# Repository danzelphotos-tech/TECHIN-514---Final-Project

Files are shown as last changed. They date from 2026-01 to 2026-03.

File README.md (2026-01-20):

# Vibe Bot – Interactive Music-Responsive Desk Robot

Vibe Bot is a wireless, music-responsive desk robot that senses ambient audio to estimate the tempo (BPM) of music and visualizes it through a mechanical gauge, animated facial display, and dynamic lighting. The system consists of a separate sensing device and display device that communicate wirelessly.

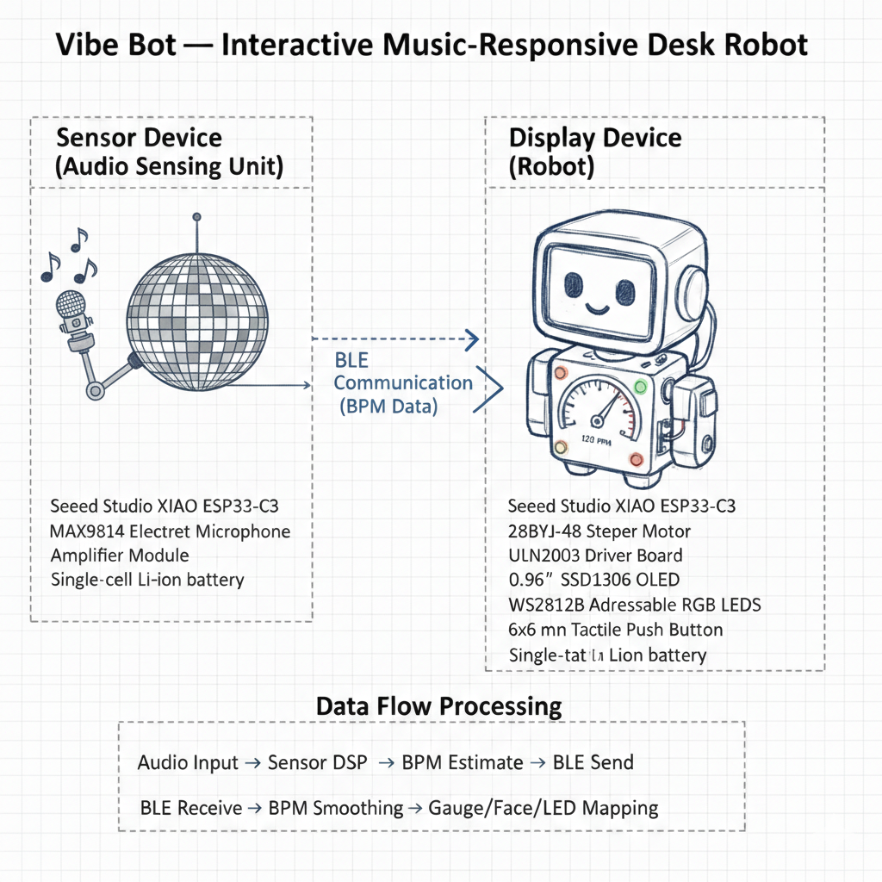
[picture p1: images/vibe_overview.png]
Overview sketch


## Sensor Device (Audio Sensing Unit)

The sensor device is a compact, battery-powered module placed near the music source. It uses a microphone to capture ambient audio, runs DSP to estimate BPM, and transmits BPM data wirelessly to the display device.

Parts (sensor device):
- Microcontroller: Seeed Studio XIAO ESP32-C3 (ESP32-C3)
- Microphone: INMP441 (I2S MEMS microphone) 

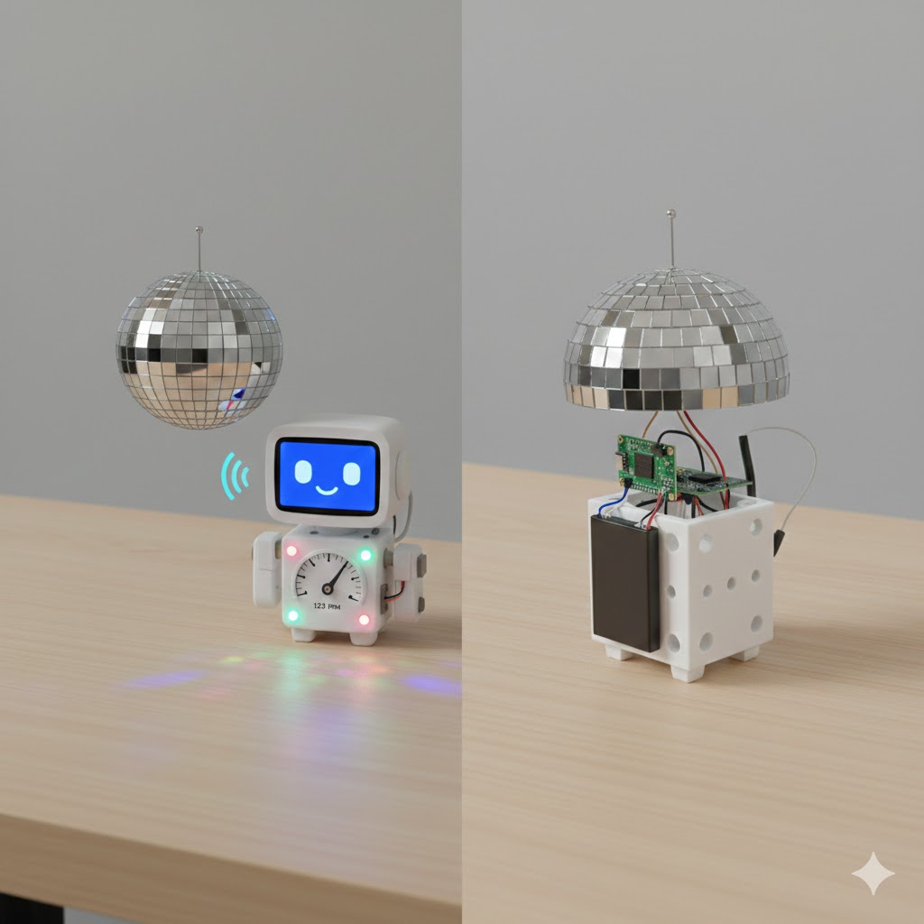
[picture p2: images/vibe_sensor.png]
Sensor device sketch


## Display Device (Robot)

The display device is a 3D-printed desktop robot that receives BPM data and visualizes it using a stepper-motor gauge needle, at least one LED, and a button for interaction (mode selection / calibration). The face is shown using an OLED display, and the LEDs provide "party lights" effects.

Parts (display device):
- Microcontroller: Seeed Studio XIAO ESP32-C3 (ESP32-C3)
- Stepper motor: 28BYJ-48
- Stepper driver: ULN2003 driver board 
- OLED: 0.96" SSD1306 I2C OLED
- LEDs: WS2812B addressable LEDs
- Button: 6x6mm tactile pushbutton

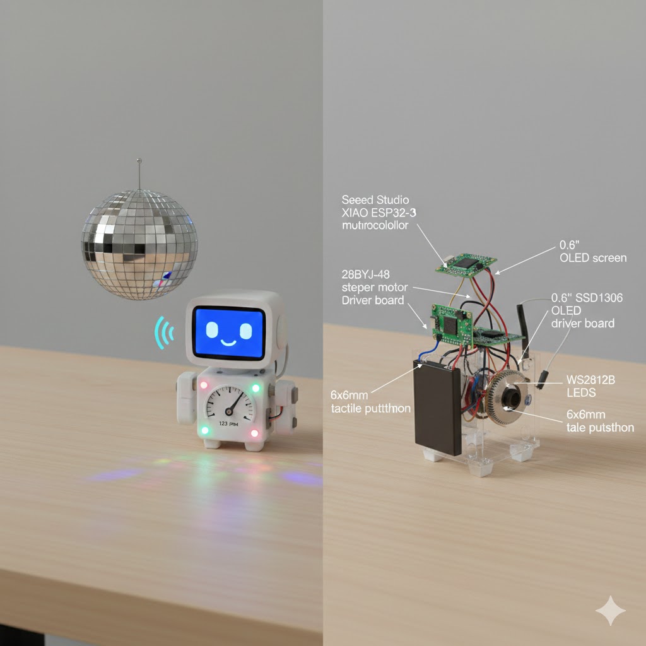
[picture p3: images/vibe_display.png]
Display device sketch


## Communication and Data Flow

The sensor device estimates BPM from audio and sends BPM (and optional confidence) over BLE to the display device. The display device smooths incoming BPM values and maps them to gauge needle position, facial animation states, and LED patterns.

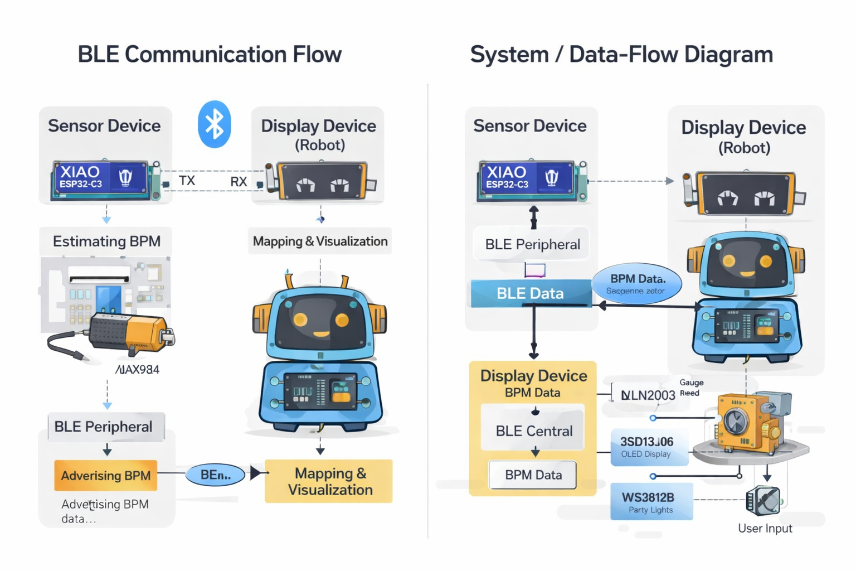
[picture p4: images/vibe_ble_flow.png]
BLE communication & diagram


## Datasheets

All component datasheets are available in the `datasheets/` folder, including:
- ESP32-C3 microcontroller
- MAX9814 microphone amplifier
- SSD1306 OLED display
- WS2812B RGB LEDs
- 28BYJ-48 stepper motor
- ULN2003 stepper driver

### Selected Components (Final)

Sensor Device:
- Microcontroller: Seeed Studio XIAO ESP32-C3
- Microphone: MAX9814 Electret Microphone Amplifier Module
- Power: Single-cell Li-ion battery

Display Device:
- Microcontroller: Seeed Studio XIAO ESP32-C3
- Stepper Motor: 28BYJ-48
- Stepper Driver: ULN2003
- Display: 0.96" SSD1306 OLED (I2C)
- LEDs: WS2812B addressable RGB LEDs
- User Input: 6x6 mm tactile push button
- Power: Single-cell Li-ion battery with onboard regulation

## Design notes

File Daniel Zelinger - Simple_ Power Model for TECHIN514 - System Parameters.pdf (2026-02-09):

System Parameters (defined by hardware) | Profiles (usage of each component mode - defined by software and usage)
form the datasheets
"off" | "sensing" | "interactive"

Processor
Active | 120 mW | 0% | 10% | 50%
Idle | 20 mW | 0% | 20% | 30%
Sleep | 1 mW | 100% | 70% | 20%
LED On | 5 mW | 0% | 5% | 50%
Sensor On | 10 mW | 0% | 10% | 80%
Idle | 2 mW | 0% | 90% | 20%
Off | 0 mW | 100% | 0% | 0%
Display On | 25 mW | 0% | 20% | 100%
Off (leakage) | 1 mW | 100% | 80% | 0%
Radio Data Rate | 300 bps | 0% | 0% | 0% | Total power in profile (mw) | Maximum Time
Standby Power | 5 mW | 98% | 95% | 90% | "off" | 7.0009696 mW | 223.9 hours
TX Power | 250 mW | 0% | 1% | 5% | "sensing" | 34.000764 mW | 46.1 hours RX Power | 120 mW | 0% | 1% | 5% | "interactive" | 125.100288 mW | 12.5 hours
16 | 7 | 1 hours/day typical usage | Effective Battery Capacity Battery | 1567.5 mW*h Capacity | 500 mAh Nominal Voltage | 3 V | Days of Use | 3.30 days Regulator Efficiency | 95% | Hours of Use | 79.18 hours
Days of use is calculated by combining the average daily energy REFLECTIONS : WHAT DID YOU LEARN FROM ANALYZING YOUR POWER. TALK ABOUT SOME POTENTIAL TRADEOFFS. | consumption across off, sensing, and interactive modes based on expected daily usage hours.

I determined the days of use by estimating how the device would typically be used each day and dividing that time between off, sensing, and interactive modes. I then calculated the average daily energy consumption using the power values of each component and how often they are active in each mode.

I chose the battery size by balancing how long the device should run with its size and cost. For the sensor device, a 500 mAh battery allows the device to operate for multiple days while staying small and lightweight. The display device uses more power because of the OLED screen and user interaction, so a larger 1000 mAh battery is more appropriate.

To improve the user experience, power consumption could be reduced by using deeper sleep modes, sending data less frequently, lowering the LED brightness, or using BLE instead of Wi Fi. These changes would require more software effort and design decisions, but they would result in longer battery life and a more comfortable and usable device.

DATASHEETS

ESP32 | | https://www.espressif.com/sites/default/files/documentation/esp32-c3_datasheet_en.pdf
LED — Standard | | https://www.vishay.com/docs/83171/tlms1100.pdf
SENSOR - INMP441 | https://invensense.tdk.com/wp-content/uploads/2015/02/INMP441.pdf Display — SSD1306 OLEDhttps://cdn-shop.adafruit.com/datasheets/SSD1306.pdf Radio (ESP32C3) | https://www.espressif.com/sites/default/files/documentation/esp32-c3_technical_reference_manual_en.pdf
Batteries | https://www.adafruit.com/product/1578
| https://www.adafruit.com/product/258

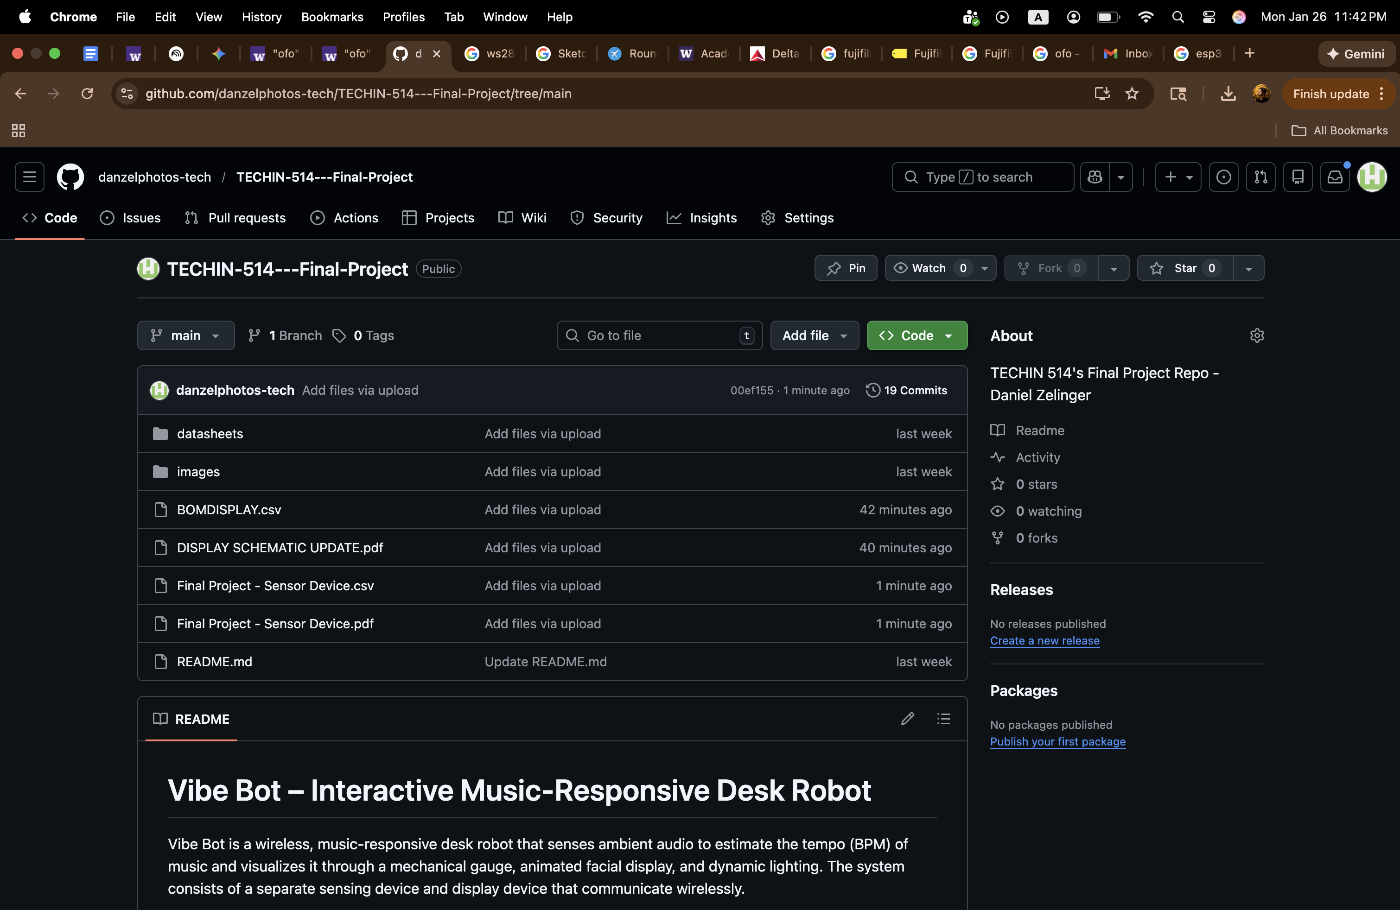
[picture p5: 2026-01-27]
GitHub SS 1:26:26.png

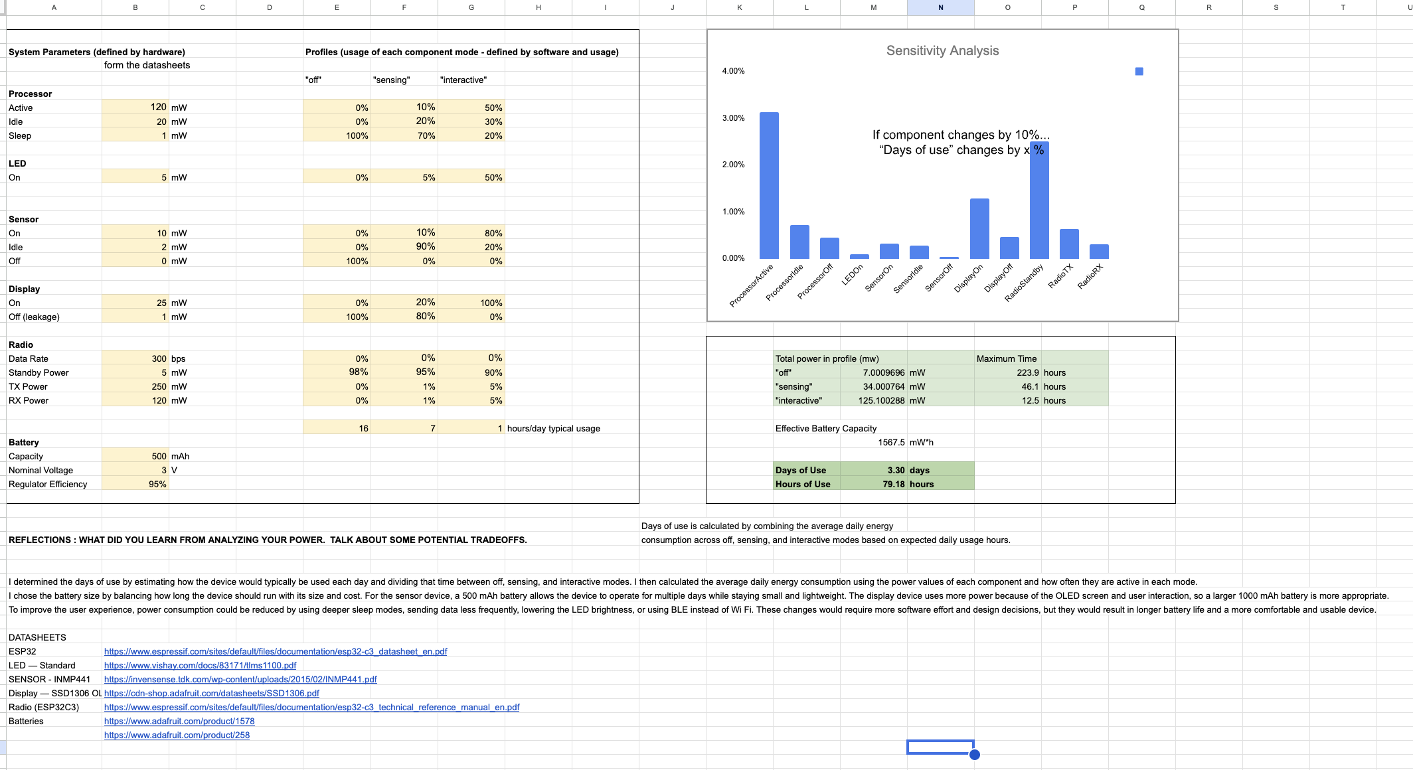
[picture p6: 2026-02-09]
Battery Life Estimate DZ.png

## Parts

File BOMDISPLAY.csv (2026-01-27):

Reference | Qty | Value | DNP | Exclude from BOM | Exclude from Board | Footprint | Datasheet
Brd1 | 1 | SSD1306
C1 | 1 | 470 µF |  |  |  |  | ~
D1 | 1 | WS2812B |  |  |  | LED_SMD:LED_WS2812B_PLCC4_5.0x5.0mm_P3.2mm | https://cdn-shop.adafruit.com/datasheets/WS2812B.pdf
J1 | 1 | Conn_01x05 |  |  |  |  | ~
J_BATT? | 1 | Conn_01x02 |  |  |  |  | ~
R1 | 1 | 330 Ω |  |  |  |  | ~
SW1 | 1 | SW_Push |  |  |  |  | ~
U1 | 1 | XIAO ESP32C3 |  |  |  | XIAO_ESP32C3:xiao_esp32c3 | https://files.seeedstudio.com/wiki/Seeed-Studio-XIAO-ESP32/esp32-c3_datasheet.pdf
U2 | 1 | ULN2003 |  |  |  |  | http://www.ti.com/lit/ds/symlink/uln2003a.pdf

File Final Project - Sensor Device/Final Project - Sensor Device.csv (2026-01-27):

Reference | Qty | Value | DNP | Exclude from BOM | Exclude from Board | Footprint | Datasheet
C_MIC? | 1 | 0.1 µF ceramic capacitor |  |  |  |  | ~
INMP441 | 1 | ~
J1 | 1 | J_BATT |  |  |  |  | ~
U1 | 1 | XIAO ESP32C3 |  |  |  | XIAO_ESP32C3:xiao_esp32c3 | https://files.seeedstudio.com/wiki/Seeed-Studio-XIAO-ESP32/esp32-c3_datasheet.pdf

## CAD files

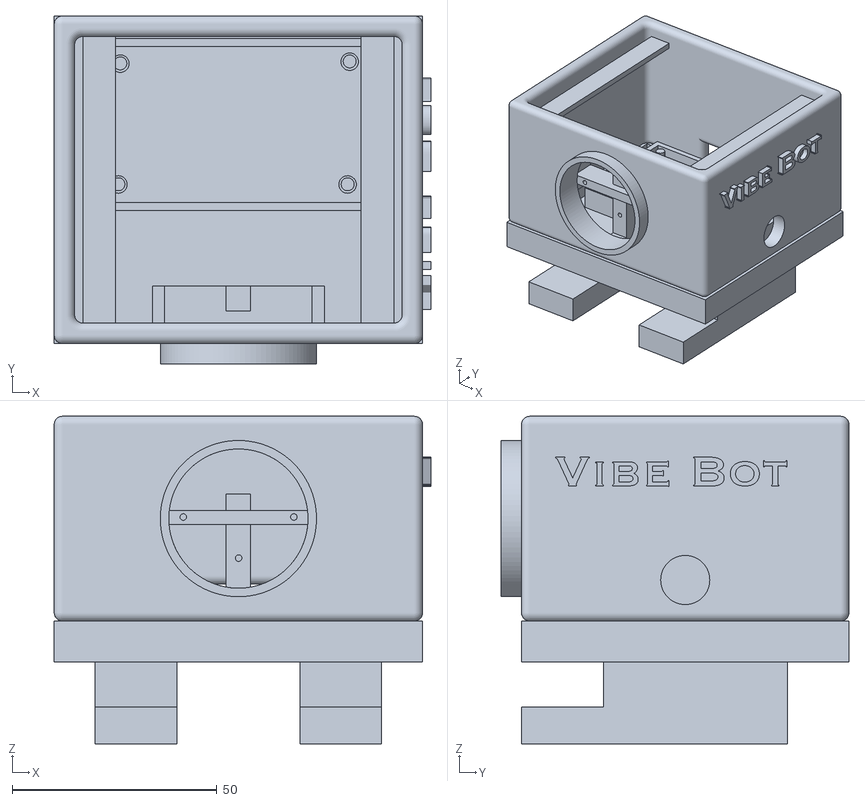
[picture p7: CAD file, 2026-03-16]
Display Device/Vibe Bot - Display Device - DZ STL.stl
92.0 x 85.0 x 80.0

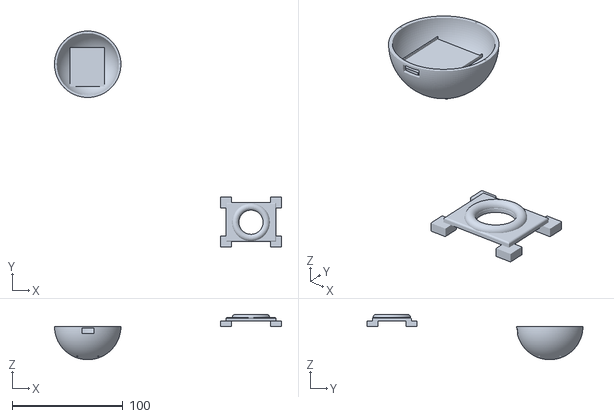
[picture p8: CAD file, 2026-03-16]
Final Project - Sensor Device/Final Project - Sensor Device Draft 1 DZ.stl
205.0 x 195.0 x 41.0

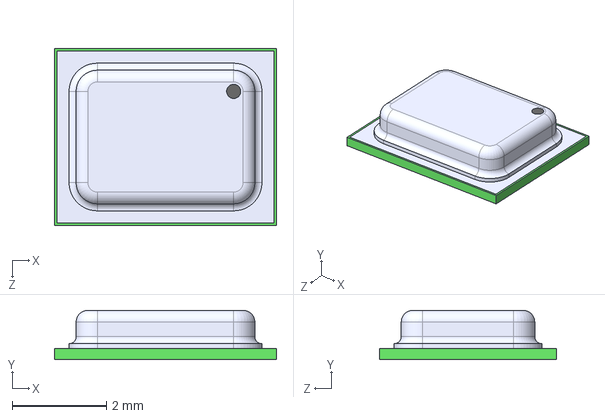
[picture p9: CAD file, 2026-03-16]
Final Project - Sensor Device/INMP441ACEZ-R7/INMP441ACEZ-R7.step
4.72 x 1.05 x 3.76 mm

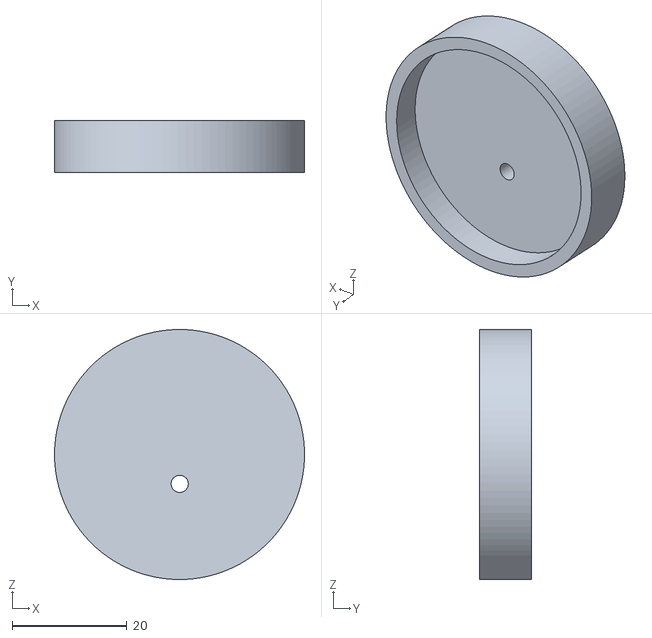
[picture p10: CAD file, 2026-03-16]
Display Device/Vibe Bot - Display Device - DZ - Motor Cap 2.stl
43.5 x 9.00 x 43.5

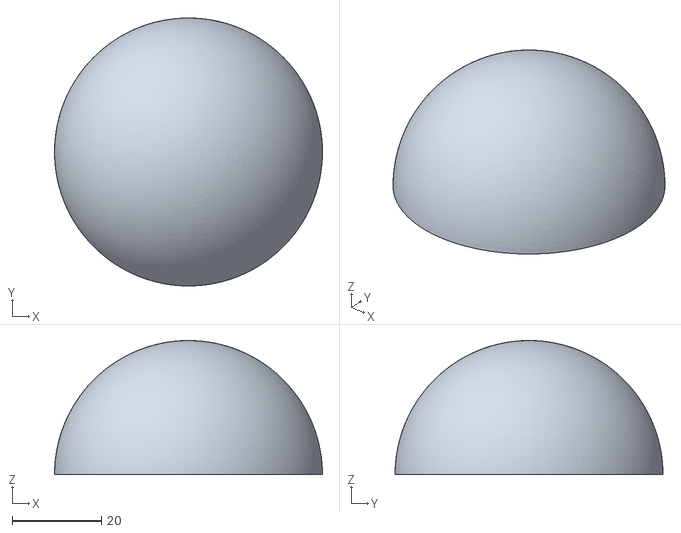
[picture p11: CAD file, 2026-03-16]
Final Project - Sensor Device/Final Project - Sensor Device Top.stl
60.0 x 60.0 x 30.0

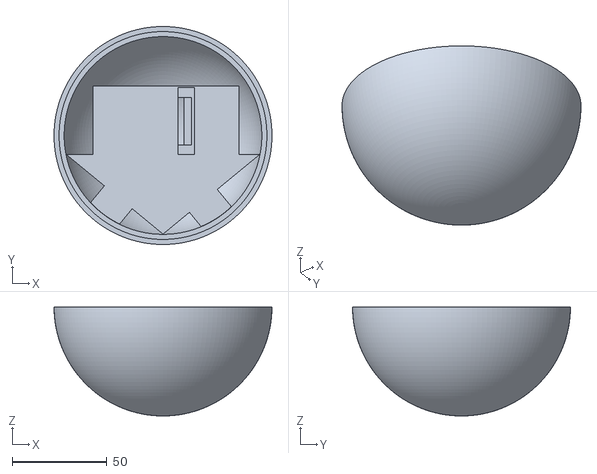
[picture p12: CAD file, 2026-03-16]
Display Device/Final Project - Sensor Device - BOTTOM.stl
115.0 x 115.0 x 57.5

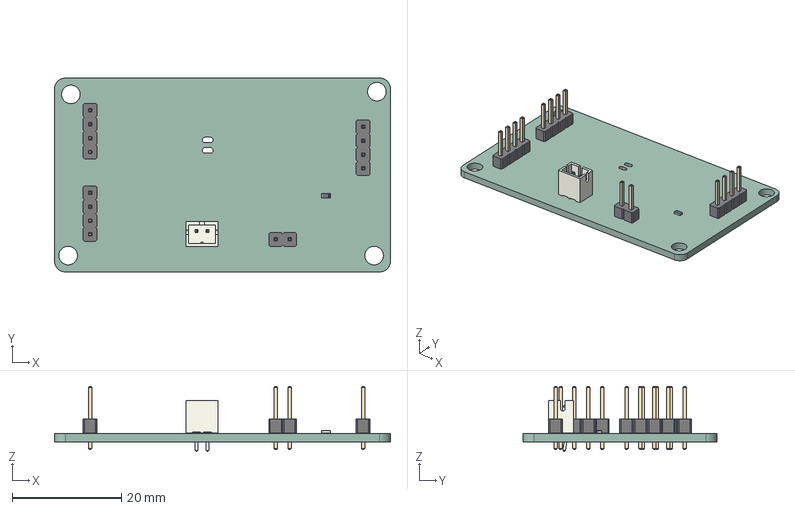
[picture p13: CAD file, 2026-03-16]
Display Device/Vibe Bot - Display Device - DZ.step
61.5 x 35.5 x 11.9 mm
PinHeader_1x04_P2.54mm_Vertical x 3
R_0603_1608Metric
PinHeader_1x02_P2.54mm_Vertical
JST_PH_B2B-PH-K_1x02_P2.00mm_Vertical
Vibe Bot - Display Device - DZ_PCB

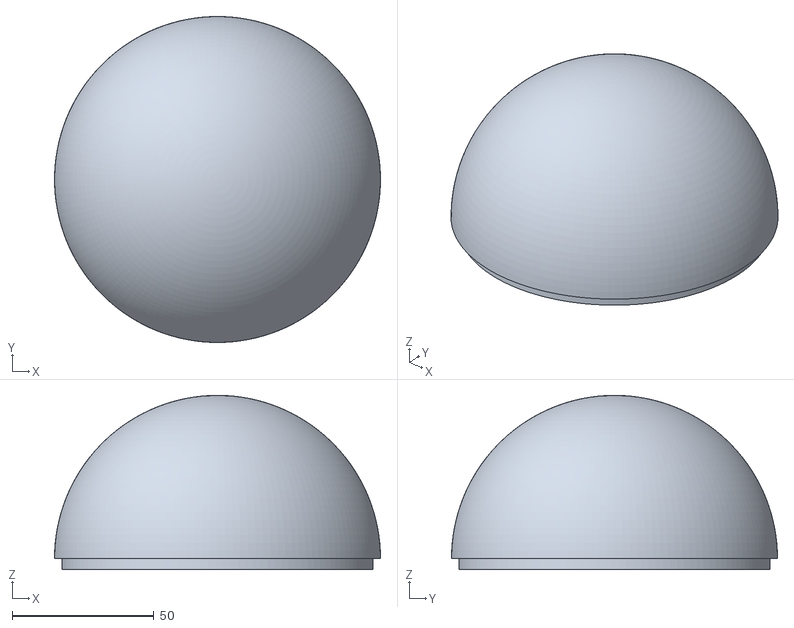
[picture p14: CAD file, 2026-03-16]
Display Device/Final Project - Sensor Device - Final Print_.stl
115.0 x 115.0 x 61.5

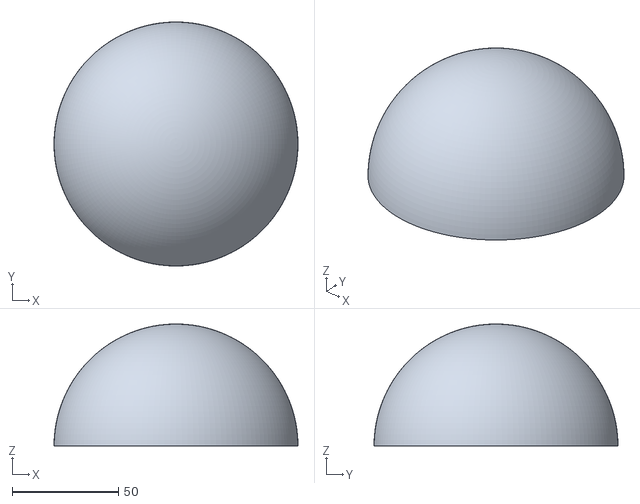
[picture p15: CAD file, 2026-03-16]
Display Device/Final Project - Sensor Device TOP.stl
115.0 x 115.0 x 57.5

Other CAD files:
Display Device/Vibe Bot - Display Device - DZ.stl
Final Project - Sensor Device/Final Project - Sensor Device FUSION F3D.f3z

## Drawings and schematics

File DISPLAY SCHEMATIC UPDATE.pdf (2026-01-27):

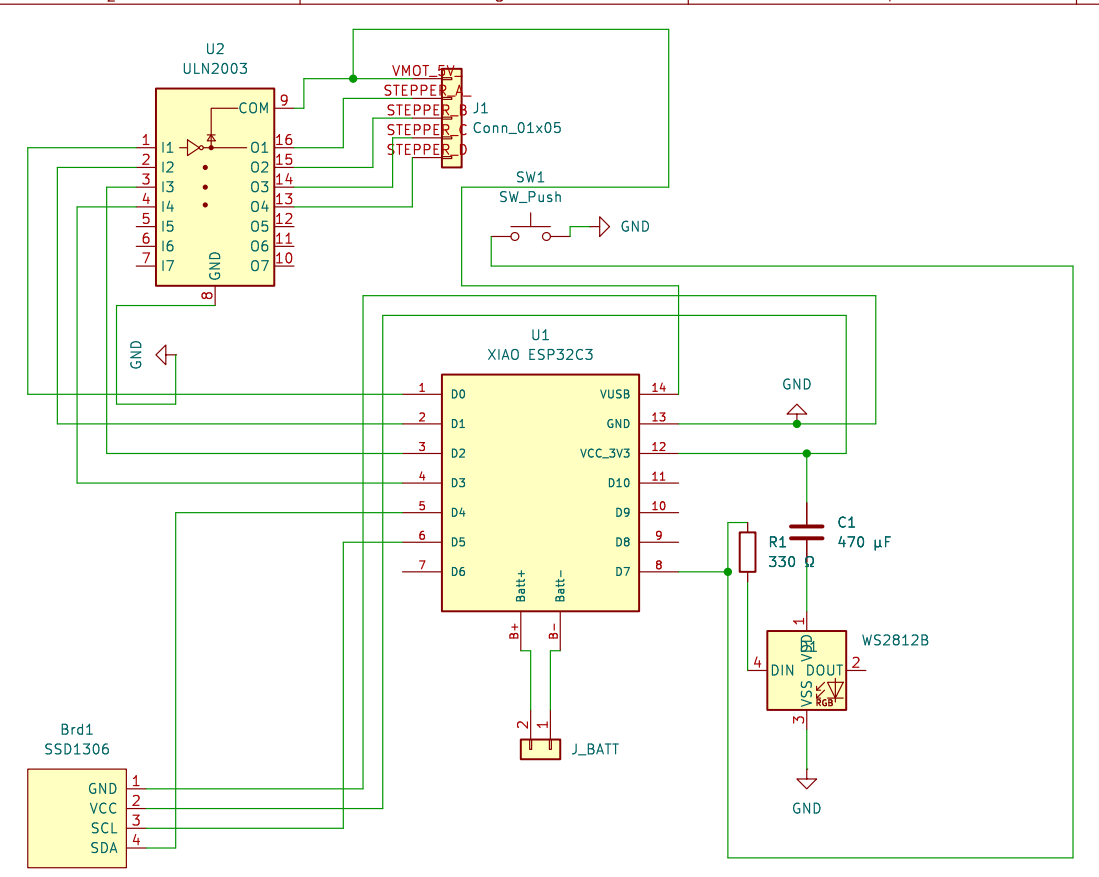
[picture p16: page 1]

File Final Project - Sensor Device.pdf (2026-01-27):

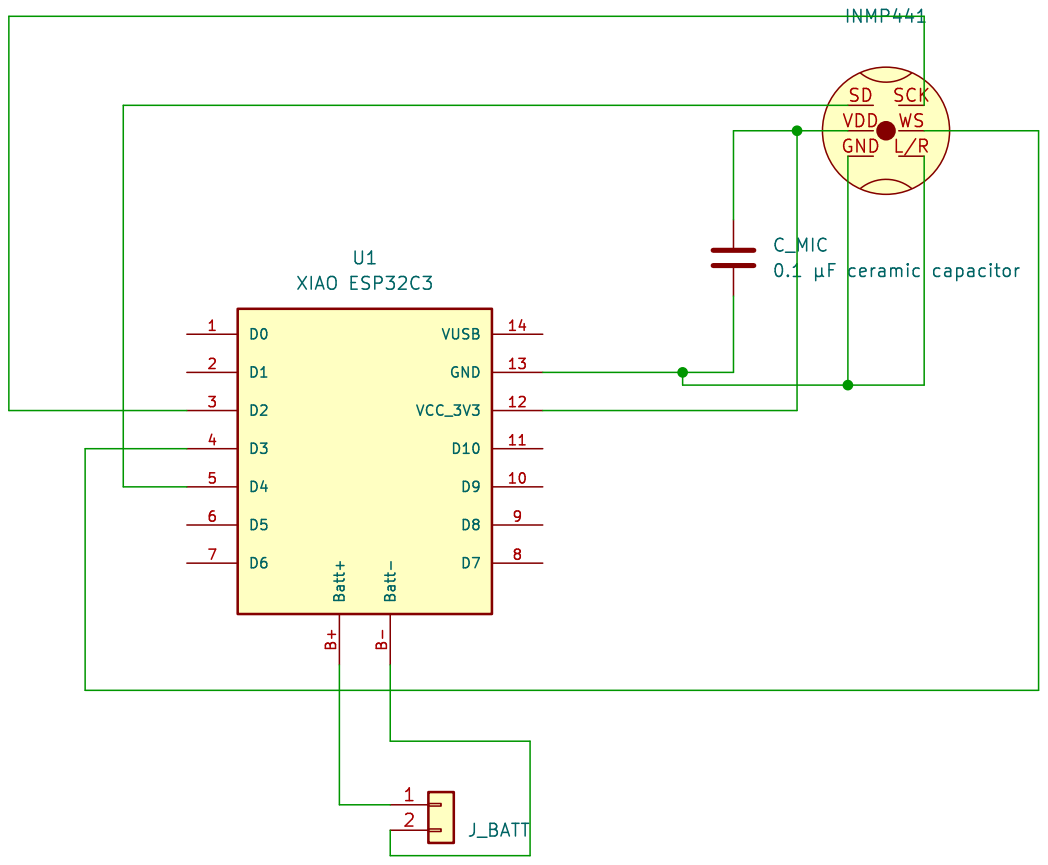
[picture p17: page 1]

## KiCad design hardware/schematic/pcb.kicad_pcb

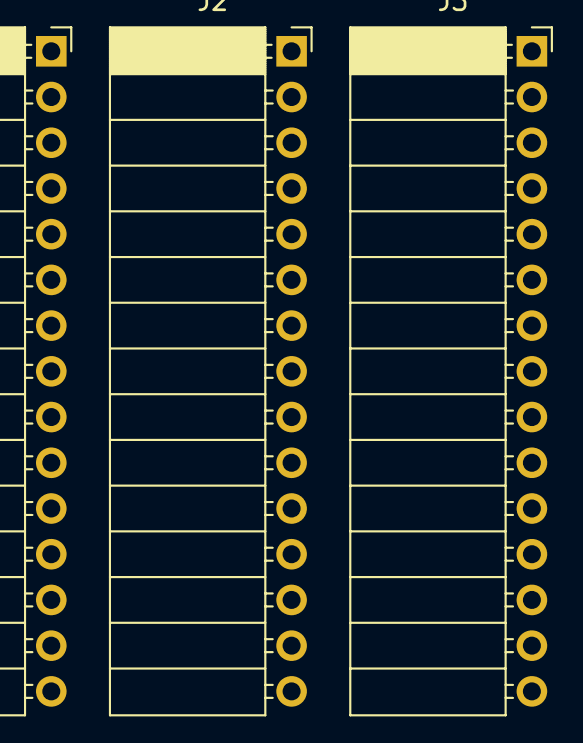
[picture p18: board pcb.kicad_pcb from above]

Board: 2 copper layers, 3 parts (0 on the bottom side), 10 nets, no tracks yet.

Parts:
J1: L; PinSocket_1x15_P2.54mm_Horizontal
J2: R; PinSocket_1x15_P2.54mm_Horizontal
J3: IR; PinSocket_1x15_P2.54mm_Horizontal

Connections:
unnamed: J1.12 (5V), J3.11 (VCC)
unnamed: J1.10 (A6), J3.10 (D8)
unnamed: J2.11 (D2), J3.3 (D1)
unnamed: J2.9 (D4), J3.4 (D2)
unnamed: J2.6 (D7), J3.5 (D3)
unnamed: J2.5 (D8), J3.6 (D4)
unnamed: J2.3 (D10), J3.7 (D5)
unnamed: J2.2 (D11), J3.8 (D6)
unnamed: J2.1 (D12), J3.9 (D7)
unnamed: J2.12 (GND), J3.1 (GND)

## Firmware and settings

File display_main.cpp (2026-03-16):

#include <Arduino.h>
#include <WiFi.h>
#include <esp_now.h>
#include <esp_idf_version.h>
#include <Wire.h>
#include <Adafruit_GFX.h>
#include <Adafruit_SSD1306.h>
#include <Adafruit_NeoPixel.h>
#include <SwitecX25.h>

// ===================== PIN CONFIG =====================
#define OLED_SDA    D4
#define OLED_SCL    D5
#define LED_PIN     D7
#define BUTTON_PIN  D8
#define MOTOR_P1    D0
#define MOTOR_P2    D1
#define MOTOR_P3    D2
#define MOTOR_P4    D3

// ===================== HARDWARE CONSTANTS =====================
#define SCREEN_W    128
#define SCREEN_H    64
#define OLED_ADDR   0x3C
#define NUM_LEDS    16
#define MOTOR_STEPS 945  // X27: 315 deg * 3 steps/deg

// ===================== PACKET (must match sensor) =====================
typedef struct __attribute__((packed)) {
  int bpm;
  int peak;
  int level;
  int beat;
  int activity;
} SensorPacket;

// ===================== VISUAL MODES =====================
enum VisualMode {
  MODE_STANDBY,
  MODE_FACE,
  MODE_BIG_BPM,
  MODE_SYNTH,
  MODE_LASER
};

static const char* modeName(VisualMode m) {
  switch (m) {
    case MODE_STANDBY: return "STANDBY";
    case MODE_FACE:    return "FACE";
    case MODE_BIG_BPM: return "BIG_BPM";
    case MODE_SYNTH:   return "SYNTH";
    case MODE_LASER:   return "LASER";
    default:           return "???";
  }
}

// Deterministic mode cycle when music is playing.
// BIG_BPM appears 3 times per 42-second cycle and cannot be skipped.
struct ModeSlot { VisualMode mode; unsigned long ms; };

static const ModeSlot MODE_CYCLE[] = {
  { MODE_BIG_BPM, 3000 },  // 0  show BPM first thing when music starts
  { MODE_FACE,    5000 },  // 1
  { MODE_FACE,    5000 },  // 2
  { MODE_BIG_BPM, 3000 },  // 3
  { MODE_FACE,    5000 },  // 4
  { MODE_SYNTH,   4000 },  // 5
  { MODE_FACE,    5000 },  // 6
  { MODE_BIG_BPM, 3000 },  // 7
  { MODE_FACE,    5000 },  // 8
  { MODE_LASER,   4000 },  // 9
};
static const int CYCLE_LEN = sizeof(MODE_CYCLE) / sizeof(MODE_CYCLE[0]);

// ===================== HARDWARE OBJECTS =====================
Adafruit_SSD1306 oled(SCREEN_W, SCREEN_H, &Wire, -1);
Adafruit_NeoPixel strip(NUM_LEDS, LED_PIN, NEO_GRB + NEO_KHZ800);
SwitecX25 motor(MOTOR_STEPS, MOTOR_P1, MOTOR_P2, MOTOR_P3, MOTOR_P4);

// ===================== RECEIVED SENSOR DATA =====================
volatile bool rxFlag = false;
SensorPacket rxBuf = {};

int bpm      = 0;
int peak     = 0;
int level    = 0;
int activity = 0;

// ===================== TIMING / STATE =====================
bool musicActive              = false;
unsigned long lastActiveMs    = 0;
unsigned long musicConfirmMs  = 0;   // when we first started seeing BPM
int musicConfirmCount         = 0;   // consecutive packets with BPM > 0
static const unsigned long MUSIC_TIMEOUT = 1500;
static const int CONFIRM_PACKETS = 6; // need ~6 consecutive BPM packets to activate

VisualMode currentMode     = MODE_STANDBY;
int cycleIdx               = 0;
unsigned long modeStartMs  = 0;

// Rave
bool raveMode              = false;
unsigned long highBpmStartMs   = 0;
unsigned long raveStartMs      = 0;
bool laserShow             = false;
unsigned long laserShowStartMs = 0;
static const unsigned long RAVE_THRESHOLD_MS = 10000;
static const unsigned long LASER_SHOW_MS     = 10000;

// Beat pulse timestamp (updated every time a beat packet arrives)
unsigned long lastBeatMs   = 0;

// Face blink animation
unsigned long lastBlinkMs    = 0;
unsigned long nextBlinkDelay = 3000;
bool eyesClosed              = false;
unsigned long blinkStartMs   = 0;

// LED fade
unsigned long ledPulseMs = 0;

// Standby screen falling notes state
static float notePos[4] = {-10, 20, 50, 80};
static float noteSpeed[4] = {0.08f, 0.12f, 0.10f, 0.09f};
static float noteX[4] = {20, 45, 80, 105};
static bool notesInitialized = false;

// ===================== ESP-NOW RECEIVE CALLBACK =====================
#if ESP_IDF_VERSION_MAJOR >= 5
void onDataRecv(const esp_now_recv_info_t *info, const uint8_t *data, int len) {
#else
void onDataRecv(const uint8_t *mac, const uint8_t *data, int len) {
#endif
  if (len == sizeof(SensorPacket)) {
    memcpy((void *)&rxBuf, data, sizeof(SensorPacket));
    rxFlag = true;
  }
}

// ===================== DRAW HELPERS =====================
static void centeredText(const char *txt, int y, int sz) {
  oled.setTextSize(sz);
  int16_t x1, y1;
  uint16_t tw, th;
  oled.getTextBounds(txt, 0, 0, &x1, &y1, &tw, &th);
  oled.setCursor((SCREEN_W - tw) / 2, y);
  oled.print(txt);
}

// ===================== STANDBY SCREEN =====================
static void drawStandby() {
  oled.clearDisplay();
  oled.setTextColor(SSD1306_WHITE);
  unsigned long now = millis();

  // --- Background: two slow synth wave lines (no fill) ---
  float phase1 = now * 0.0008f;
  float phase2 = now * 0.0012f;
  for (int x = 0; x < SCREEN_W; x++) {
    int y1 = 54 + (int)(6.0f * sinf(x * 0.06f + phase1));
    int y2 = 58 + (int)(4.0f * sinf(x * 0.09f + phase2));
    y1 = constrain(y1, 0, SCREEN_H - 1);
    y2 = constrain(y2, 0, SCREEN_H - 1);
    oled.drawPixel(x, y1, SSD1306_WHITE);
    oled.drawPixel(x, y2, SSD1306_WHITE);
  }

  // --- Falling music notes ---
  if (!notesInitialized) {
    notesInitialized = true;
    for (int i = 0; i < 4; i++) {
      notePos[i] = -10.0f + i * 18.0f;
      noteX[i] = 8 + random(SCREEN_W - 16);
    }
  }

  for (int i = 0; i < 4; i++) {
    notePos[i] += noteSpeed[i];
    if (notePos[i] > SCREEN_H + 8) {
      notePos[i] = -8;
      noteX[i] = 8 + random(SCREEN_W - 16);
    }
    int ny = (int)notePos[i];
    int nx = (int)noteX[i];
    if (ny >= -4 && ny < SCREEN_H) {
      // Note head (filled oval)
      oled.fillCircle(nx, ny, 2, SSD1306_WHITE);
      // Stem going up
      oled.drawFastVLine(nx + 2, ny - 6, 7, SSD1306_WHITE);
      // Flag
      oled.drawPixel(nx + 3, ny - 6, SSD1306_WHITE);
      oled.drawPixel(nx + 4, ny - 5, SSD1306_WHITE);
    }
  }

  // --- Text (drawn last so it's always on top) ---
  centeredText("Let's", 10, 2);
  centeredText("VIBE", 30, 3);

  // Animated dots
  int dots = (now / 500) % 4;
  for (int i = 0; i < dots; i++)
    oled.fillCircle(48 + i * 12, 58, 2, SSD1306_WHITE);

  oled.display();
}

// ===================== BIG BPM SCREEN =====================
static void drawBigBpm() {
  oled.clearDisplay();
  oled.setTextColor(SSD1306_WHITE);

  int cx = SCREEN_W / 2;
  int cy = SCREEN_H / 2 - 6;

  bool recentBeat = (millis() - lastBeatMs) < 250;
  if (recentBeat) {
    int t = millis() - lastBeatMs;
    oled.drawCircle(cx, cy, 18 + t / 8,  SSD1306_WHITE);
    oled.drawCircle(cx, cy, 10 + t / 12, SSD1306_WHITE);
  } else {
    float breath = sinf((millis() % 2000) * 3.14159f / 1000.0f);
    oled.drawCircle(cx, cy, 26 + (int)(breath * 3), SSD1306_WHITE);
  }

  char buf[8];
  snprintf(buf, sizeof(buf), "%d", bpm);
  oled.setTextSize(4);
  int16_t x1, y1;
  uint16_t tw, th;
  oled.getTextBounds(buf, 0, 0, &x1, &y1, &tw, &th);
  oled.setCursor((SCREEN_W - tw) / 2, cy - th / 2);
  oled.print(buf);

  centeredText("BPM", 54, 1);
  oled.display();
}

// ===================== FACE SCREEN =====================
static void drawFace(bool rave) {
  oled.clearDisplay();
  oled.setTextColor(SSD1306_WHITE);
  unsigned long now = millis();

  bool recentBeat = (now - lastBeatMs) < 180;

  // --- Blink state machine ---
  if (!eyesClosed && now - lastBlinkMs > nextBlinkDelay) {
    eyesClosed   = true;
    blinkStartMs = now;
  }
  if (eyesClosed && now - blinkStartMs > 150) {
    eyesClosed     = false;
    lastBlinkMs    = now;
    nextBlinkDelay = 2000 + random(3000);
  }

  // --- Eyes with pupils ---
  const int eyeW = 24, eyeY = 8;
  int eyeH = eyesClosed ? 3 : 16;
  const int lx = 14, rx = 90;
  oled.fillRoundRect(lx, eyeY, eyeW, eyeH, 3, SSD1306_WHITE);
  oled.fillRoundRect(rx, eyeY, eyeW, eyeH, 3, SSD1306_WHITE);

  if (!eyesClosed) {
    int pupilR = 4;
    int lookX = (int)(2.0f * sinf(now * 0.0008f));
    int pupilY = eyeY + eyeH / 2;
    oled.fillCircle(lx + eyeW / 2 + lookX, pupilY, pupilR, SSD1306_BLACK);
    oled.fillCircle(rx + eyeW / 2 + lookX, pupilY, pupilR, SSD1306_BLACK);
  }

  // --- Eyebrows that bounce on beat ---
  int baseTilt = rave ? 7 : 3;
  int beatBounce = recentBeat ? 4 : 0;
  int browY = eyeY - 4 - beatBounce;

  for (int t = 0; t < 2; t++) {
    oled.drawLine(lx - 2,        browY - baseTilt + t,
                  lx + eyeW + 2, browY + t,             SSD1306_WHITE);
    oled.drawLine(rx - 2,        browY + t,
                  rx + eyeW + 2, browY - baseTilt + t,   SSD1306_WHITE);
  }

  // --- Mouth / teeth visualizer ---
  const int mouthY = 34, mouthH = 28;
  const int nTeeth = 8, gap = 2;
  int tw = (SCREEN_W - 4 - (nTeeth - 1) * gap) / nTeeth;
  int totalW = nTeeth * tw + (nTeeth - 1) * gap;
  int startX = (SCREEN_W - totalW) / 2;

  oled.drawRect(startX - 2, mouthY - 1, totalW + 4, mouthH + 2, SSD1306_WHITE);

  static const int shape[] = {-3, 1, -1, 4, 2, -2, 3, 0};

  for (int i = 0; i < nTeeth; i++) {
    int h;
    if (recentBeat) {
      h = mouthH - 2 + (shape[i] % 3);
    } else {
      int base = map(constrain(level, 0, 400), 0, 400, 4, mouthH - 6);
      h = base + shape[i];
    }
    h = constrain(h, 2, mouthH - 1);
    int x = startX + i * (tw + gap);
    oled.fillRect(x, mouthY + mouthH - h, tw, h, SSD1306_WHITE);
  }

  oled.display();
}

// ===================== SYNTH WAVE SCREEN =====================
static void drawSynthWave(bool rave) {
  oled.clearDisplay();

  int waves = rave ? 4 : 2;

  // Wave scroll speed scales with BPM: faster BPM = faster waves
  float bpmFactor = constrain(bpm, 60, 200) / 120.0f;
  float speed = (rave ? 0.006f : 0.003f) * bpmFactor;
  float freqBase = 0.05f + 0.02f * bpmFactor;

  bool recentBeat = (millis() - lastBeatMs) < 150;
  float beatBoost = recentBeat ? 6.0f : 0.0f;

  for (int w = 0; w < waves; w++) {
    float freq  = freqBase + w * 0.025f;
    float phase = millis() * speed + w * 1.5f;
    int yBase   = SCREEN_H / 2 + (w - waves / 2) * 10;
    int prevY   = -1;

    for (int x = 0; x < SCREEN_W; x++) {
      float amp = 14.0f + beatBoost + 5.0f * sinf(millis() * 0.001f + w);
      int y = yBase + (int)(amp * sinf(x * freq + phase));
      y = constrain(y, 0, SCREEN_H - 1);
      oled.drawPixel(x, y, SSD1306_WHITE);

      if (prevY >= 0 && abs(y - prevY) > 1) {
        int lo = min(y, prevY), hi = max(y, prevY);
        for (int ly = lo; ly <= hi; ly++)
          oled.drawPixel(x, ly, SSD1306_WHITE);
      }
      prevY = y;
    }
  }

  oled.setTextColor(SSD1306_WHITE);
  oled.setTextSize(1);
  oled.setCursor(2, 2);
  oled.printf("%d BPM", bpm);
  oled.display();
}

// ===================== LASER SCREEN =====================
static void drawLaser(bool rave) {
  oled.clearDisplay();
  unsigned long now = millis();
  bool pulse = (now - lastBeatMs) < 200;

  // --- Animation 1: zoom rings (expanding/contracting circles) ---
  float breathPeriod = 1500.0f;
  float t = fmodf(now, breathPeriod) / breathPeriod;
  int cx = SCREEN_W / 2;
  int cy = SCREEN_H / 2;
  int nRings = rave ? 6 : 4;

  for (int i = 0; i < nRings; i++) {
    float phase = fmodf(t + (float)i / nRings, 1.0f);
    int r = (int)(phase * 40);
    if (pulse) r += 4;
    if (r > 2 && r < 50)
      oled.drawCircle(cx, cy, r, SSD1306_WHITE);
  }

  // --- Animation 2: bottom-up laser beams (concert POV) ---
  int nBeams = rave ? 10 : 6;
  float sway = now * (rave ? 0.003f : 0.0015f);

  for (int i = 0; i < nBeams; i++) {
    float spread = -0.8f + (float)i / (nBeams - 1) * 1.6f;
    float angle  = spread + 0.15f * sinf(sway + i * 0.9f);

    int baseX = SCREEN_W / 2 + (int)((SCREEN_W / 2) * sinf(spread * 0.5f));
    int topX  = baseX + (int)(SCREEN_H * tanf(angle));
    int topY  = pulse ? -4 : 0;

    oled.drawLine(baseX, SCREEN_H - 1, topX, topY, SSD1306_WHITE);
    if (rave)
      oled.drawLine(baseX + 1, SCREEN_H - 1, topX + 1, topY, SSD1306_WHITE);
  }

  // --- Ground line ---
  oled.drawFastHLine(0, SCREEN_H - 1, SCREEN_W, SSD1306_WHITE);

  oled.setTextColor(SSD1306_WHITE);
  oled.setTextSize(1);
  oled.setCursor(2, 2);
  oled.printf("%d BPM", bpm);
  oled.display();
}

// ===================== LED UPDATE =====================
static void updateLeds() {
  unsigned long now = millis();
  unsigned long elapsed = now - ledPulseMs;

  if (!musicActive) {
    // Standby: rainbow scroll matching the OLED wave speed
    uint16_t hueBase = (uint16_t)(now * 0.0008f * 65536.0f) % 65536;
    for (int i = 0; i < NUM_LEDS; i++) {
      uint16_t hue = hueBase + (i * 65536 / NUM_LEDS);
      strip.setPixelColor(i, strip.ColorHSV(hue, 255, 40));  // dim rainbow
    }
    strip.show();
    return;
  }

  // Beat pulse: sharp flash that fades quickly
  uint8_t beatBr = 0;
  if (elapsed < 200) {
    // Exponential decay for snappier feel
    float t = elapsed / 200.0f;
    beatBr = (uint8_t)(255 * (1.0f - t * t));
  }

  // Base brightness from audio level (subtle background glow)
  uint8_t baseBr = map(constrain(peak, 0, 2000), 0, 2000, 5, 40);
  
  // Activity boost: adds brightness on peaks
  uint8_t activityBr = map(constrain(activity, 0, 1000), 0, 1000, 0, 30);

  // Combine: beat flash + base + activity
  uint8_t totalBr = min(255, beatBr + baseBr + activityBr);

  // Color based on BPM
  uint32_t c;
  if (bpm < 80) {
    // Teal/cyan
    c = strip.Color(0, totalBr, totalBr / 2);
  } else if (bpm < 120) {
    // Blue
    c = strip.Color(0, totalBr / 3, totalBr);
  } else {
    // Magenta/pink
    c = strip.Color(totalBr, 0, totalBr / 3);
  }

  // Apply with slight variation for visual interest
  for (int i = 0; i < NUM_LEDS; i++) {
    // Center LEDs get full brightness, edges slightly dimmer
    float pos = (float)i / (NUM_LEDS - 1);
    float fade = 0.7f + 0.3f * (1.0f - abs(pos - 0.5f) * 2.0f);
    uint8_t r = (uint8_t)(((c >> 16) & 0xFF) * fade);
    uint8_t g = (uint8_t)(((c >> 8) & 0xFF) * fade);
    uint8_t b = (uint8_t)((c & 0xFF) * fade);
    strip.setPixelColor(i, strip.Color(r, g, b));
  }
  strip.show();
}

// ===================== MOTOR UPDATE =====================
static void updateMotor() {
  int target = map(constrain(bpm, 0, 200), 0, 200, 0, MOTOR_STEPS - 1);
  motor.setPosition(target);
  motor.update();
}

// ===================== SETUP =====================
void setup() {
  Serial.begin(115200);
  delay(1000);
  Serial.println("\n========== Vibe Bot Display ==========");

  pinMode(BUTTON_PIN, INPUT_PULLUP);

  Wire.begin(OLED_SDA, OLED_SCL);
  if (!oled.begin(SSD1306_SWITCHCAPVCC, OLED_ADDR)) {
    Serial.println("[DISP] OLED FAIL");
    while (true) delay(100);
  }
  oled.clearDisplay();
  oled.display();
  Serial.println("[DISP] OLED OK");

  strip.begin();
  strip.setBrightness(80);
  strip.show();
  Serial.println("[DISP] LEDs OK");

  motor.zero();
  Serial.println("[DISP] Motor OK");

  WiFi.mode(WIFI_STA);
  WiFi.disconnect();
  delay(200);
  Serial.print("[DISP] MAC: ");
  Serial.println(WiFi.macAddress());

  if (esp_now_init() != ESP_OK) {
    Serial.println("[DISP] ESP-NOW FAIL");
    while (true) delay(100);
  }
  esp_now_register_recv_cb(onDataRecv);
  Serial.println("[DISP] ESP-NOW ready – waiting for sensor");

  currentMode  = MODE_STANDBY;
  modeStartMs  = millis();
  lastActiveMs = 0;
}

// ===================== MAIN LOOP =====================
void loop() {
  unsigned long now = millis();

  // ---- Consume incoming packet ----
  if (rxFlag) {
    rxFlag   = false;
    bpm      = rxBuf.bpm;
    peak     = rxBuf.peak;
    level    = rxBuf.level;
    activity = rxBuf.activity;

    if (rxBuf.beat) {
      lastBeatMs = now;
      ledPulseMs = now;
    }

    // Music confirmation: require multiple consecutive packets with real BPM
    if (rxBuf.bpm > 30) {
      musicConfirmCount++;
      if (musicConfirmCount >= CONFIRM_PACKETS)
        lastActiveMs = now;
    } else {
      musicConfirmCount = 0;
    }
  }

  // ---- Music-active with hysteresis ----
  bool wasActive = musicActive;
  musicActive = (lastActiveMs > 0) && (now - lastActiveMs < MUSIC_TIMEOUT);

  // ==========================================================
  //  STATE MACHINE
  // ==========================================================

  if (!musicActive) {
    // ---- NO MUSIC -> standby ----
    if (currentMode != MODE_STANDBY) {
      currentMode = MODE_STANDBY;
      cycleIdx    = 0;
      raveMode    = false;
      laserShow   = false;
      Serial.println("[DISP] -> STANDBY");
    }

  } else {
    // ---- MUSIC ACTIVE ----

    // Returning from standby / first packet -> start the cycle
    if (!wasActive || currentMode == MODE_STANDBY) {
      cycleIdx       = 0;
      modeStartMs    = now;
      currentMode    = MODE_CYCLE[0].mode;
      raveMode       = false;
      highBpmStartMs = 0;
      laserShow      = false;
      Serial.printf("[DISP] Music ON -> %s\n", modeName(currentMode));
    }

    // ---- Rave detection (BPM > 120 for 10 s) ----
    if (bpm > 120) {
      if (highBpmStartMs == 0) highBpmStartMs = now;
      if (!raveMode && (now - highBpmStartMs >= RAVE_THRESHOLD_MS)) {
        raveMode    = true;
        raveStartMs = now;
        Serial.println("[DISP] RAVE ON");
      }
    } else {
      highBpmStartMs = 0;
      if (raveMode) {
        raveMode  = false;
        laserShow = false;
        Serial.println("[DISP] Rave OFF");
      }
    }

    // ---- Laser-show override (10 s into rave) ----
    if (raveMode && !laserShow && (now - raveStartMs >= RAVE_THRESHOLD_MS)) {
      laserShow        = true;
      laserShowStartMs = now;
      Serial.println("[DISP] LASER SHOW START");
    }
    if (laserShow) {
      if (now - laserShowStartMs < LASER_SHOW_MS)
        currentMode = MODE_LASER;
      else {
        laserShow   = false;
        modeStartMs = now;
        Serial.println("[DISP] LASER SHOW END");
      }
    }

    // ---- Normal cycle advance (skipped while laser show owns the screen) ----
    if (!laserShow) {
      if (now - modeStartMs >= MODE_CYCLE[cycleIdx].ms) {
        cycleIdx    = (cycleIdx + 1) % CYCLE_LEN;
        modeStartMs = now;
        currentMode = MODE_CYCLE[cycleIdx].mode;
        Serial.printf("[DISP] -> %s [%d] %lums\n",
                      modeName(currentMode), cycleIdx, MODE_CYCLE[cycleIdx].ms);
      }
    }
  }

  // ==========================================================
  //  DRAW
  // ==========================================================
  switch (currentMode) {
    case MODE_STANDBY: drawStandby();           break;
    case MODE_FACE:    drawFace(raveMode);      break;
    case MODE_BIG_BPM: drawBigBpm();            break;
    case MODE_SYNTH:   drawSynthWave(raveMode); break;
    case MODE_LASER:   drawLaser(raveMode);     break;
  }

  // ==========================================================
  //  PERIPHERALS
  // ==========================================================
  updateLeds();
  updateMotor();

  // ==========================================================
  //  DEBUG LOG (every 500 ms)
  // ==========================================================
  static unsigned long lastLog = 0;
  if (now - lastLog > 500) {
    lastLog = now;
    Serial.printf("[DISP] mode=%-8s bpm=%3d pk=%4d lv=%3d act=%3d music=%d rave=%d laser=%d\n",
                  modeName(currentMode), bpm, peak, level, activity,
                  musicActive, raveMode, laserShow);
  }

  delay(16);
}

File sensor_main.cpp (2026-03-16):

#include <Arduino.h>
#include <WiFi.h>
#include <esp_now.h>
#include <driver/i2s.h>

// ===================== PIN CONFIG =====================
#define I2S_WS   D1
#define I2S_SCK  D0
#define I2S_SD   D2

// ===================== AUDIO CONFIG =====================
#define SAMPLE_RATE     16000
#define BUFFER_SAMPLES  512

// ===================== ESP-NOW =====================
// Replace with your display device's MAC address
uint8_t displayMAC[] = {0x1C, 0xDB, 0xD4, 0x75, 0xAA, 0xD4};

// ===================== PACKET =====================
typedef struct __attribute__((packed)) {
  int bpm;
  int peak;
  int level;
  int beat;
  int activity;
} SensorPacket;

// ===================== GLOBALS =====================
int32_t audioBuffer[BUFFER_SAMPLES];
SensorPacket packet;

// Envelope followers for onset detection
float envFast  = 0.0f;
float envSlow  = 0.0f;
float onsetEnv = 0.0f;
float onsetAvg = 0.0f;

// Beat tracking
unsigned long lastBeatMs = 0;
bool beatLatch = false;

#define BEAT_HISTORY 8
unsigned long beatIntervals[BEAT_HISTORY] = {0};
int beatIdx = 0;

// BPM
int bpmSmoothed = 0;
int bpmLocked   = 0;            // once locked, holds steady
bool bpmIsLocked = false;
unsigned long bpmLockTime = 0;  // when we locked
unsigned long lastMusicMs = 0;
unsigned long lastAudioMs = 0;  // any audio energy (not just "music")

// Beat confidence
int consecutiveBeats = 0;
static const int MIN_BEATS_TO_LOCK = 4;

// Relock: count how many consecutive candidates disagree with lock
int relockCount = 0;
static const int RELOCK_THRESHOLD = 8; // need 8 consecutive outliers to re-lock

// ===================== HELPERS =====================
int clamp(int v, int lo, int hi) {
  return v < lo ? lo : (v > hi ? hi : v);
}

void clearBeatHistory() {
  for (int i = 0; i < BEAT_HISTORY; i++) beatIntervals[i] = 0;
  beatIdx = 0;
}

void pushInterval(unsigned long ms) {
  if (ms >= 230 && ms <= 2000) {
    beatIntervals[beatIdx] = ms;
    beatIdx = (beatIdx + 1) % BEAT_HISTORY;
  }
}

int computeBpm() {
  unsigned long now = millis();

  if (lastBeatMs == 0 || (now - lastBeatMs) > 3000)
    return 0;

  // Collect valid intervals
  unsigned long valid[BEAT_HISTORY];
  int n = 0;
  for (int i = 0; i < BEAT_HISTORY; i++) {
    if (beatIntervals[i] >= 230 && beatIntervals[i] <= 2000)
      valid[n++] = beatIntervals[i];
  }
  if (n < 2) return 0;

  // Find minimum interval — the shortest gap is most likely correct
  // because missed beats can only create longer gaps, never shorter.
  unsigned long minVal = valid[0];
  for (int i = 1; i < n; i++)
    if (valid[i] < minVal) minVal = valid[i];

  // Reject anything > 1.5x the minimum (likely a missed beat)
  unsigned long maxOk = minVal + (minVal / 2);

  unsigned long sum = 0;
  int count = 0;
  for (int i = 0; i < n; i++) {
    if (valid[i] <= maxOk) {
      sum += valid[i];
      count++;
    }
  }
  if (count < 2) return 0;

  float avg = (float)sum / count;

  // Consistency check: reject if intervals vary too much (speech = random)
  float variance = 0;
  for (int i = 0; i < n; i++) {
    if (valid[i] <= maxOk) {
      float diff = (float)valid[i] - avg;
      variance += diff * diff;
    }
  }
  variance /= count;
  float stddev = sqrtf(variance);
  if (stddev / avg > 0.25f) return 0;  // coefficient of variation > 25% = not music

  int raw = (int)(60000.0f / avg);

  if (raw > 0 && raw < 70) raw *= 2;
  if (raw > 180) raw /= 2;

  return clamp(raw, 0, 230);
}

// ===================== I2S SETUP =====================
void setupI2S() {
  i2s_config_t cfg = {};
  cfg.mode             = (i2s_mode_t)(I2S_MODE_MASTER | I2S_MODE_RX);
  cfg.sample_rate      = SAMPLE_RATE;
  cfg.bits_per_sample  = I2S_BITS_PER_SAMPLE_32BIT;
  cfg.channel_format   = I2S_CHANNEL_FMT_ONLY_LEFT;
  cfg.communication_format = I2S_COMM_FORMAT_I2S;
  cfg.intr_alloc_flags = ESP_INTR_FLAG_LEVEL1;
  cfg.dma_buf_count    = 4;
  cfg.dma_buf_len      = 256;
  cfg.use_apll         = false;

  i2s_pin_config_t pins = {};
  pins.bck_io_num   = I2S_SCK;
  pins.ws_io_num    = I2S_WS;
  pins.data_out_num = -1;
  pins.data_in_num  = I2S_SD;

  i2s_driver_install(I2S_NUM_0, &cfg, 0, NULL);
  i2s_set_pin(I2S_NUM_0, &pins);
  i2s_zero_dma_buffer(I2S_NUM_0);
}

// ===================== ESP-NOW SETUP =====================
void setupEspNow() {
  WiFi.mode(WIFI_STA);
  WiFi.disconnect();
  delay(200);

  Serial.print("[SENSOR] MAC: ");
  Serial.println(WiFi.macAddress());

  if (esp_now_init() != ESP_OK) {
    Serial.println("[SENSOR] ESP-NOW init FAILED");
    while (true) delay(100);
  }

  esp_now_peer_info_t peer = {};
  memcpy(peer.peer_addr, displayMAC, 6);
  peer.channel = 0;
  peer.encrypt = false;

  if (esp_now_add_peer(&peer) != ESP_OK) {
    Serial.println("[SENSOR] Add peer FAILED");
    while (true) delay(100);
  }

  Serial.println("[SENSOR] ESP-NOW ready");
}

// ===================== BEAT DETECTION =====================
bool detectBeat(int peak, int level) {
  unsigned long now = millis();

  envFast = 0.30f * envFast + 0.70f * peak;   // near-instant attack
  envSlow = 0.995f * envSlow + 0.005f * peak;

  float onset = max(0.0f, envFast - envSlow);
  onsetEnv = 0.35f * onsetEnv + 0.65f * onset;  // minimal smoothing
  onsetAvg = 0.995f * onsetAvg + 0.005f * onsetEnv;

  float thresh = onsetAvg * 1.4f + 50.0f;
  bool energyOk = (level > 120 && peak > 600);
  bool timeOk   = (now - lastBeatMs) > 230;

  bool beat = false;
  if (energyOk && onsetEnv > thresh && timeOk && !beatLatch) {
    beat = true;
    if (lastBeatMs > 0) pushInterval(now - lastBeatMs);
    lastBeatMs = now;
    beatLatch = true;
  }

  if (onsetEnv < thresh * 0.55f) beatLatch = false;  // faster release

  return beat;
}

// ===================== SETUP =====================
void setup() {
  Serial.begin(115200);
  delay(1000);
  Serial.println("\n========== Vibe Bot Sensor ==========");

  setupI2S();
  setupEspNow();
}
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
